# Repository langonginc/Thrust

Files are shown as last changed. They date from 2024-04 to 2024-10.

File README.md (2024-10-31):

# Horizontal Thrust Measuring Stage

A stage to measure horizontral thrust generated by rocket engine.

This is a project created by students in The Aviation Club of the [Second High School Attached to Beijing Normal University](https://www.shsbnu.net/index.html).

[推力台说明手册(中文版) | Chinese version](https://github.com/langonginc/Thrust/blob/main/README.pdf)

SolidWorks 3D Model

[Video from bilibili](https://www.bilibili.com/video/BV1fC411E7s8/?share_source=copy_web&vd_source=09f47ca71ce9a13b053114acdf5cffeb) 

# Highlights

We use Arduino Mega 2560 and HX711 to record and store the magnitude of the thrust into the program, and graph the associated function (force @ time).

- **0-20kg** measuring range _(maximum value not to exceed 30kg)_
- 30-50mm engine diameter fit
- 10Hz sample rate ([#1](https://github.com/langonginc/ForceTestStand/issues/1) We really need your help to increase it)
- Real-time display
- Serial port writing
- ~~SD card data writing~~

# Theory

Presure -> Sensors -> HX711 -> Arduino.

Pressure sensors generate a voltage by sensing pressure. Sensitive voltage value is 1mv, which means if I apply a force of `1kg`, it produces a voltage of `1mV` (for 0-10kg sensor).

HX711 will firstly amplify the voltage generated by the pressure sensor, since the voltage is too small. Then it will convert the analog signals (amplified voltage values) to digital signals (ad values).

After that, Arduino will get the digital signals (ad values). We then scale the digital signal to fit the pressure.

## Why We Use HX711

Based on Avia Semiconductor’s patented technology, HX711 is a precision 24-bit analog-to-digital converter (ADC) designed for weigh scales and industrial control applications to interface directly with a bridge sensor.

The input multiplexer selects either Channel A or B differential input to the low-noise programmable gain amplifier (PGA). Channel A can be programmed with a gain of 128 or 64, corresponding to a full-scale differential input voltage of ±20mV or ±40mV respectively, when a 5V supply is connected to AVDD analog power supply pin. Channel B has a fixed gain of 32. On-chip power supply regulator eliminates the need for an external supply regulator to provide analog power for the ADC and the sensor. Clock input is flexible. It can be from an external clock source, a crystal, or the on-chip oscillator that does not require any external component. On-chip power-on-reset circuitry simplifies digital interface initialization.

There is no programming needed for the internal registers. All controls to the HX711 are through the pins.

> We are using the channel A (input voltage of ±20mV).

## How HX711 works

The HX711 communicates with the microcontroller in serial communication mode consisting of pins SCK and DOUT. When DOUT goes from high to low, SCK inputs 25 pulses at a time to read the 24-bit A/D conversion data into the microcontroller and selects the input channel and gain for the next conversion on the 25th clock pulse.

# Getting Started

## Building Framework

Based on the Solidworks 3D model, the framework can be built with the following items.

| Item | Details | Quantity | Image |
| :----- | :----- | :----- | :----: |
| European Standard Aluminum Profiles 3030 | Length 400mm | 2 |  |
| European Standard Aluminum Profiles 3030 | Length 360mm | 1 | Same as above |
| European Standard Aluminum Profiles 3030 | Length 300mm | 5 | Same as above |
| European Standard Aluminum Profiles 3030 | Length 200mm | 1 | Same as above |
| European Standard Slider Nuts 3030 | M4 | About 20 |  |
| European Standard Angle Fittings 3030 | | 16 |  |
| Steel shaft ø8 | 300mm | 2 |  |
| Shaft fixing bracket ø8 | | 4 |  |
| Carriage slider ø8 | | 4 |  |
| Tray base plate _(Laser cut by myself)_ | From `plate.dwg` | 1 |  |

> SolidWorks 2022, AutoCAD 2024 (DWG 2018)

## Wiring the Arduino Board

Wire the Arduino board and components using DuPont wires according to the following table.

| Item | Image | Reference link |
| :----- | :----- | :----- |
| HX711 chip + Pressure sensor |  | [Link](https://detail.tmall.com/item.htm?id=570644601916) |
| TM1650 4-digit digital tube display module |  | |

**Arduino - HX711**

| Arduino Pin | HX711 Pin |
| :----: | :----: |
| 5V | VCC |
| GND | GND |
| 2 | SCK |
| 3 | DOUT |

**HX711 - Pressure sensors**

| HX711 Pin | Sensors Wire |
| :----: | :----: |
| E+ | Red |
| E- | Black |
| A- | White |
| A+ | Green |

**Arduino - Micro SD Card Adapter**

_We just removed this component as its low writing speed._

| Arduino Pin | HX711 Pin |
| :----: | :----: |
| 5V | VCC |
| GND | GND |
| 50 | MISO |
| 51 | MOSI |
| 52 | SCK |
| 53 | CS |

> The communication between the microcontroller and the SD card uses SPI, which takes place on digital pins 11, 12, and 13 (on most Arduino boards) or 50, 51, and 52 (Arduino Mega). Additionally, another pin must be used to select the SD card. This can be the hardware SS pin - pin 10 (on most Arduino boards) or pin 53 (on the Mega) - or another pin specified in the call to SD.begin(). Note that even if you don't use the hardware SS pin, it must be left as an output or the SD library won't work.
>
> --Arduino SD libarary

## Uploading Code to Arduino Board

Download `main.ino` and open it in Arduino IDE ([Link](https://www.arduino.cc/en/software)).

Plug in your Arduino. Then, click the "upload" button.

## Getting Data

Click `Tools - Serial Monitor` to check the results.



## Analysing Data

Copy the results getting from the serial monitor, which are array of integers (e.g. `101, 123.4, 111, 114.5, 121, 514.5, ...`) to the third line of `graph.py`.

```python
originalData = [ Paste Data To Here ]     # Notice: delete the last comma ',' !!!
```

Run the code, you will get a graph that is the associated function (force @ time).

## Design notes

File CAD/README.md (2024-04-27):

# CAD files

These files are written with AutoCAD 2024 and saved in format DWG 2018.

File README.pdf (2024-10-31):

北京师范⼤学第⼆附属中学 航模社 | ⽔平推⼒测定台 v1.4

# ⽔平推⼒测定台说明⼿册

# 任务要求

实现 10 公⽄⽔平推⼒精确测定，通过推⼒数据绘制⼒关于时间（F/t）图像。

# 实现思路

使⽤欧标 3030 铝⽅管作为框架材料，将 304 不锈钢材质托盘放置在滑轨上，并 将产⽣推⼒的物品通过夹具固定在托盘上。产⽣推⼒时，带动滑块向前推测⼒计进⾏ 测⼒。测⼒计由 10 公⽄测⼒模块组成，使⽤ Arduino + HX711 模块处理数据，并使⽤ Python 程序⽣成相关图像。

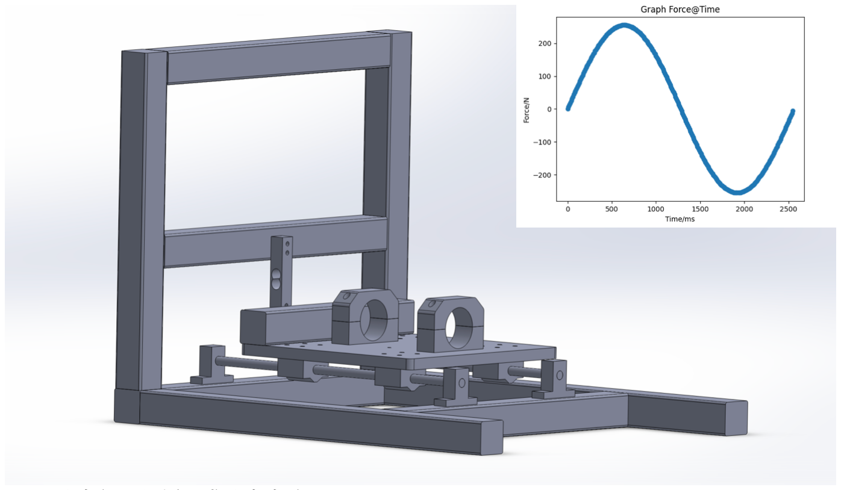
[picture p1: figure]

测试台还包括两盏⼤灯提供照明。

# 物品清单

铝⽅管
欧标 3030 400mm | 2 个
欧标 3030 360mm | 1 个
欧标 3030 300mm | 5 个
欧标 3030 200mm | 1 个
欧标 3030 直⻆连接⻆件 | 16 套
欧标 3030 滑块螺⺟ | ⽀架 8+托盘前挡 2+测⼒计前板 2+侧板 2 个
欧标 3030 端盖 | 8 个

轴
钢制轴 ø8 300mm | 2 根 | 有
轴固定⽀架 ø8 | 4 个
厢式滑块 ø8 | 4 个
限位器 ø8 | 1 个

螺丝
M4*10（滑块） | 16 根
M4*10（固定⽀架） | 8 根
M4*15（前挡） | 1 根

电路元件
测⼒计（含 HX711） | 1 套
Arduino Mega 2560 | 1 个
Arduino Micro SD 卡组件 | 1 个 | 删去，保留拓展能⼒
数码管显示屏 | 1 个
杜邦线 | 若⼲

夹具
夹具（3D 打印） | 2 套

灯具
灯具（遮光罩 3D 打印） 2 套

其他⾃制
托盘（⽊板/亚克⼒） | 1 个 | 切割
前档板 | 1 个 | 切割
测⼒计防撞板 | 1 个 | 切割

# 实现技术参数

⻓宽⾼ | 430*360*330
承重能⼒ | 约 50kg
测量推⼒范围 | 0.02kg-20kg
最⼤安全推⼒ | 30kg
承载物直径 | 38-52mm
承载物⻓度（建议） | 40-200mm
承载物⻓度（理论最⼤） | 300mm
理论最⼩采样率 | 10ms/次
实际采样率 | 100ms/次

# 原理解释

由压⼒传感器采集信号，并通过 HX711 芯⽚信号放⼤、AD 转换实现⽤数字信号 输⼊进 Arduino 单⽚机进⾏处理，最终将数据存储并显示。
HX711 是⼀款专为⾼精度电⼦秤⽽设计的 24 位 A/D 转换器芯⽚。与同类型其它 芯⽚相⽐，该芯⽚集成了包括稳压电源、⽚内时钟振荡器等其它同类型芯⽚所需要的 外围电路，具有集成度⾼、响应速度快、抗⼲扰性强等优点。降低了电⼦秤的整机成 本，提⾼了整机的性能和可靠性。该芯⽚与后端 MCU 芯⽚的接⼝和编程⾮常简单， 所有控制信号由管脚驱动，⽆需对芯⽚内部的寄存器编程。输⼊选择开关可任意选取 通道 A 或通道 B，与其内部的低噪声可编程放⼤器相连。通道 A 的可编程增益为 128 或 64，对应的满额度差分输⼊信号幅值分别为±20mV 或±40mV。通道 B 则为固定的 64 增益，⽤于系统参数检测。芯⽚内提供的稳压电源可以直接向外部传感器和芯⽚内 的 A/D 转换器提供电源，系统板上⽆需另外的模拟电源。芯⽚内的时钟振荡器不需要 任何外接器件。上电⾃动复位功能简化了开机的初始化过程。
HX711 与单⽚机的通讯由管脚 SCK 和 DOUT 组成的串⾏通讯模式。当 DOUT 从 ⾼电平变成低电平后，SCK ⼀次输⼊ 25 个脉冲，将 24 位 A/D 转换数据读⼊单⽚机， 并在第 25 个时钟脉冲选择好下次转换的输⼊通道和增益。
使⽤⽅法

打开 Arduino IDE 的串⼝监视器，并向 Arduino 通电，等待显示屏显示“8888”，此 时系统初始化完毕。
轻推测⼒计⼀下，使屏幕显示“0000”。松开后，屏幕会开始倒计时 3 秒。等到显 示“0”时，开始测⼒。
将产⽣推⼒的物体⽔平推测⼒计，当测⼒计记录到⼒时，屏幕会显示⼒的⼤⼩， 当⼒⼩于 10000g 时单位为克（g），超过时显示单位为千克（kg），此时会向 SD 卡内 写⼊数据。
测⼒完成后，相反⽅向拉动测⼒模块，使之产⽣超过负 1000 克的⼒，然后切断 电源即可。

# 总结反思

当前版本已经过⼿压⼒测试，考核范围 0-33kg，顺利通过。 本产品出⾊地完成了推⼒测定任务，在 1.5s 内完成了 16 个采样（左图），绘制出 了拟合曲线，并进⾏了积分运算，得出了推⼒曲线（右图）。

数据采集

AD 转换 | 单⽚机处理 | 数码管显示 串⼝输出
信号放⼤

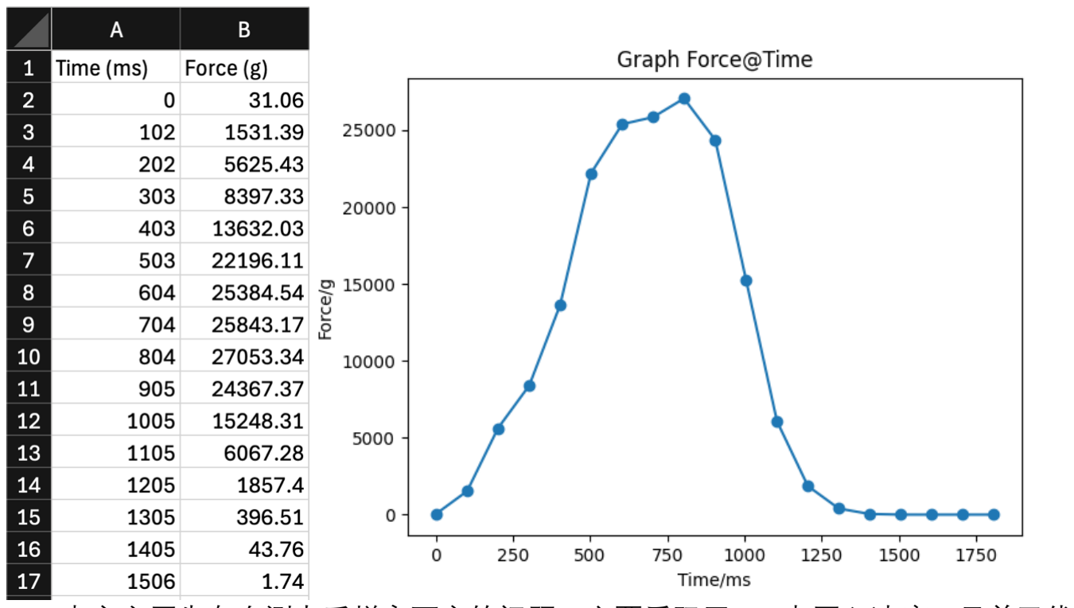
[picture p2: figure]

本⽅案原先存在测⼒采样率不⾼的问题，主要受限于 SD 卡写⼊速度，⽬前已优 化，仅使⽤串⼝通信⽅案。⽽串⼝通信⽅案的弊端在于应⽤时必须使⽤电脑有线连接 本产品，不如原⽅案便捷。

# 附加信息

本设计⽅案由北京师范⼤学第⼆附属中学航模社设计实施，以上内容仅供参考。 本设计⽅案同时发布于 GitHub 平台，在 langonginc/ForceTestStand (https://github.com/langonginc/ForceTestStand) 仓库托管，基
于 GPL-3.0 协议开源，修改或商⽤需遵守 GPL-3.0 协议的规定。

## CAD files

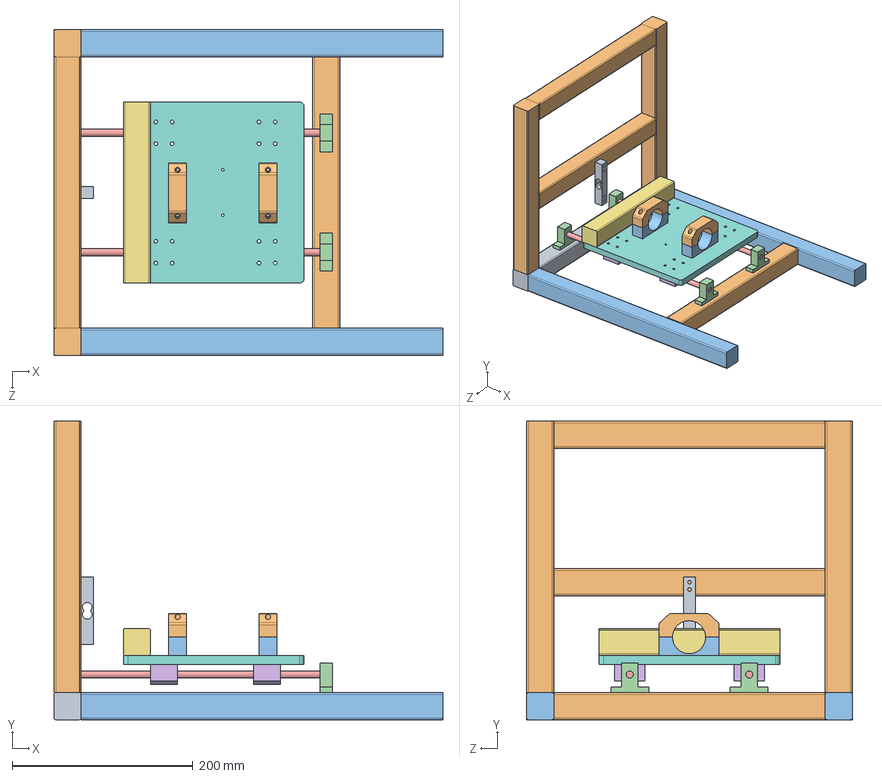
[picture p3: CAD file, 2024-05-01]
SolidWorks 3D Model/platform.SLDASM
430.0 x 330.0 x 360.0 mm
3030M-2-360
3030M-2-300 x 5
3030M-2-400 x 2
foot-8 x 4
stick-8-400 x 2
slider x 4
3030M-2-200
plate-new
sensor
fixture-upper x 2
fixture-lower x 2

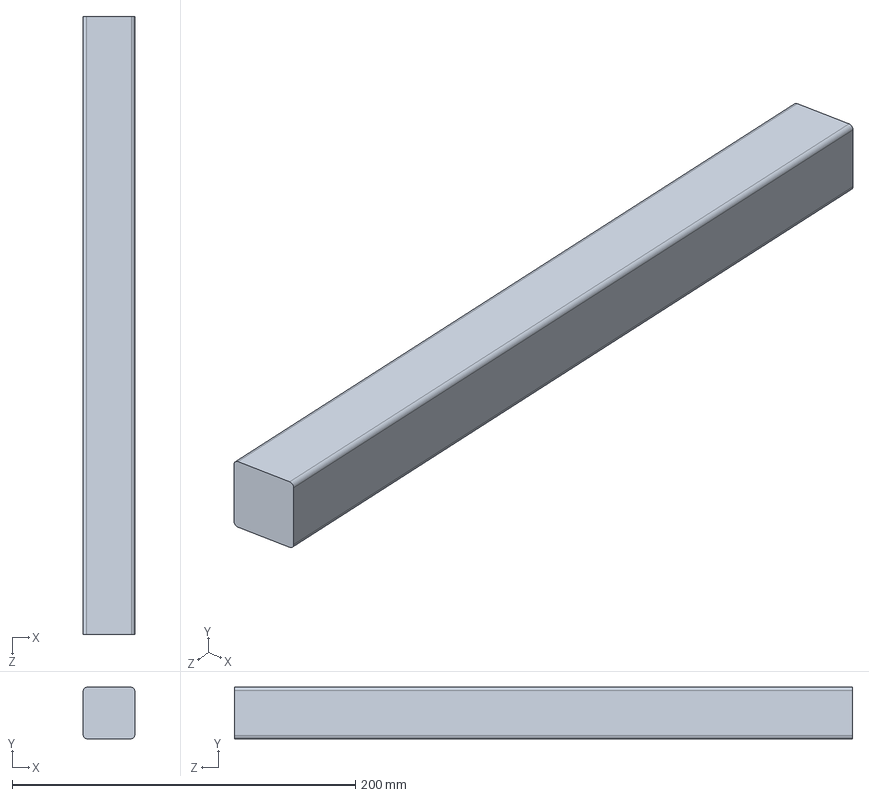
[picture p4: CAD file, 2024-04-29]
SolidWorks 3D Model/3030M-2-360.SLDPRT
30.0 x 30.0 x 360.0 mm

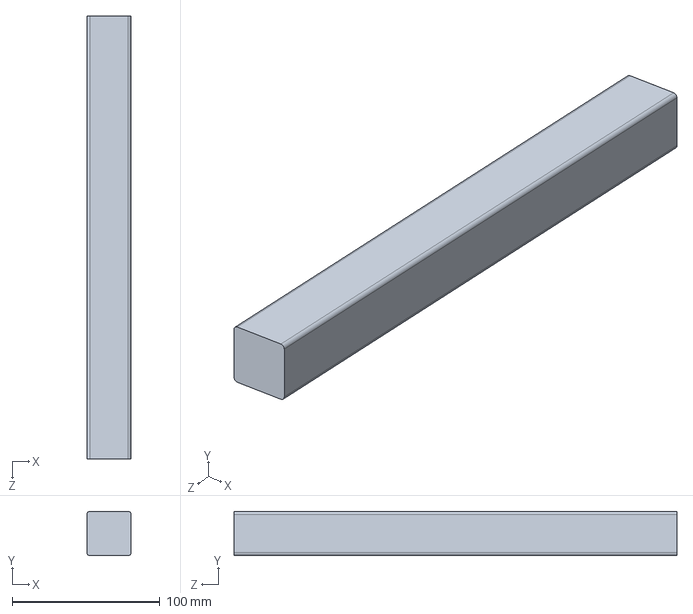
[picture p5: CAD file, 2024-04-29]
SolidWorks 3D Model/3030M-2-300.SLDPRT
30.0 x 30.0 x 300.0 mm

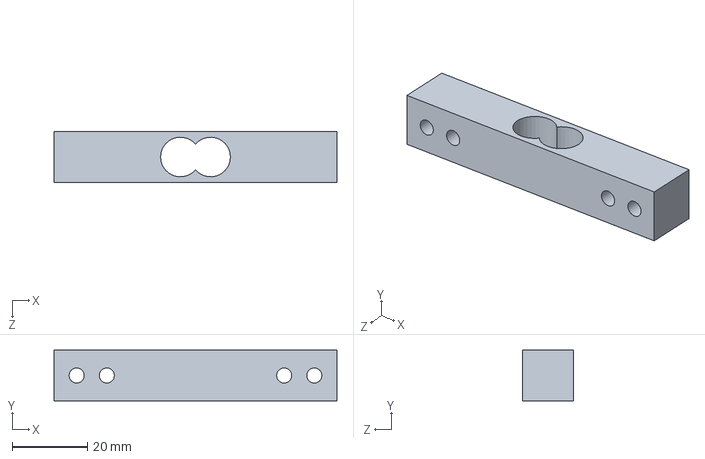
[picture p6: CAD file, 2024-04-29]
SolidWorks 3D Model/sensor.SLDPRT
75.0 x 13.5 x 13.5 mm

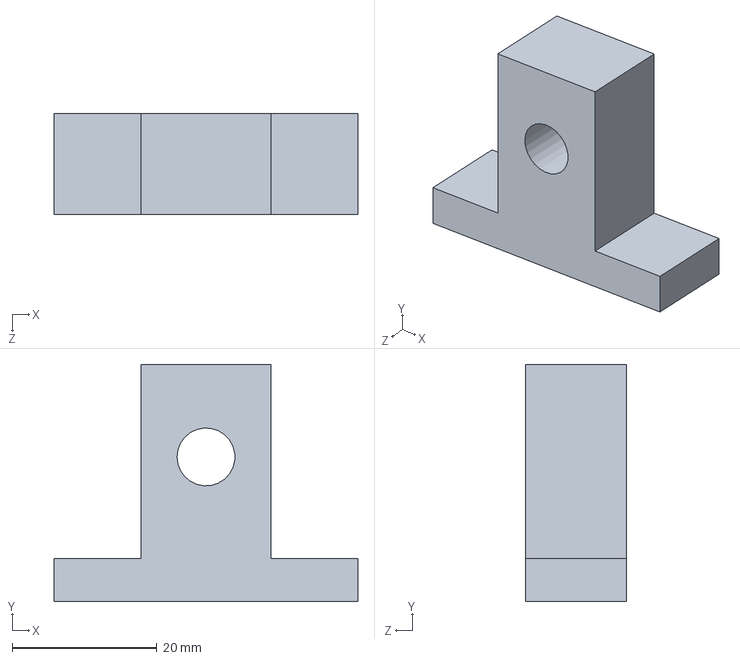
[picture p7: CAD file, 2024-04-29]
SolidWorks 3D Model/foot-8.SLDPRT
42.0 x 32.8 x 14.0 mm

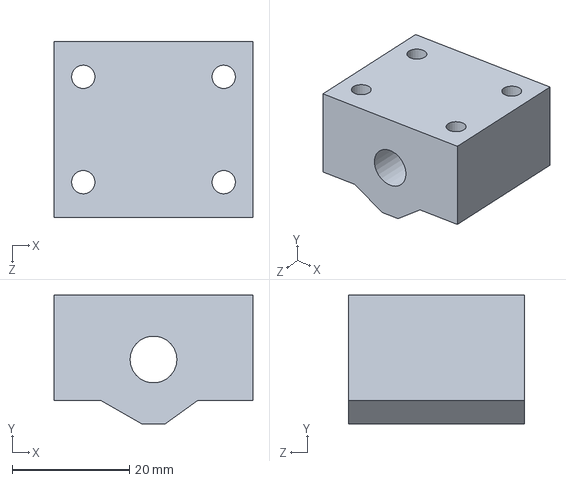
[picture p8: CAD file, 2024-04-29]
SolidWorks 3D Model/slider.SLDPRT
34.0 x 22.0 x 30.0 mm

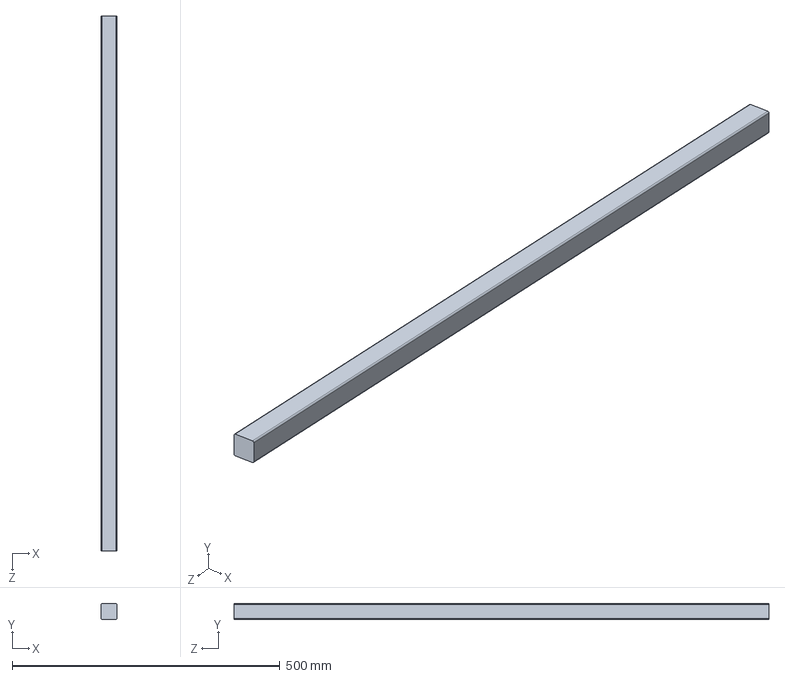
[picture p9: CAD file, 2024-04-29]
SolidWorks 3D Model/3030M-2-1m.SLDPRT
30.0 x 30.0 x 1000.0 mm

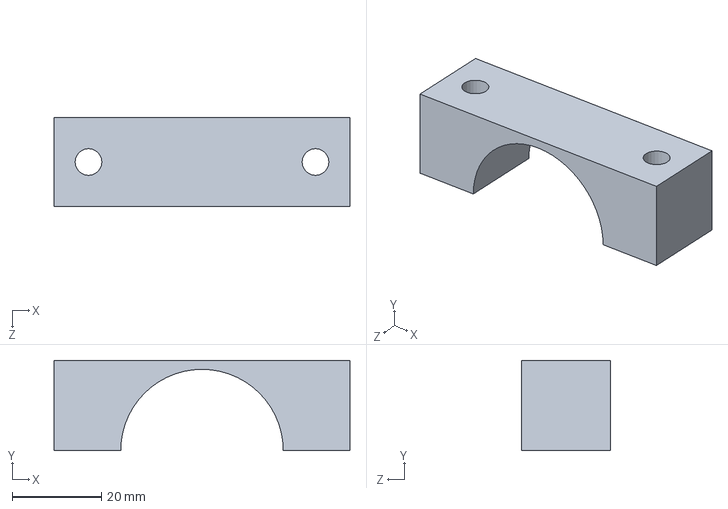
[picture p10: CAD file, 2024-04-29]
SolidWorks 3D Model/fixture-lower.SLDPRT
66.5 x 20.2 x 20.0 mm

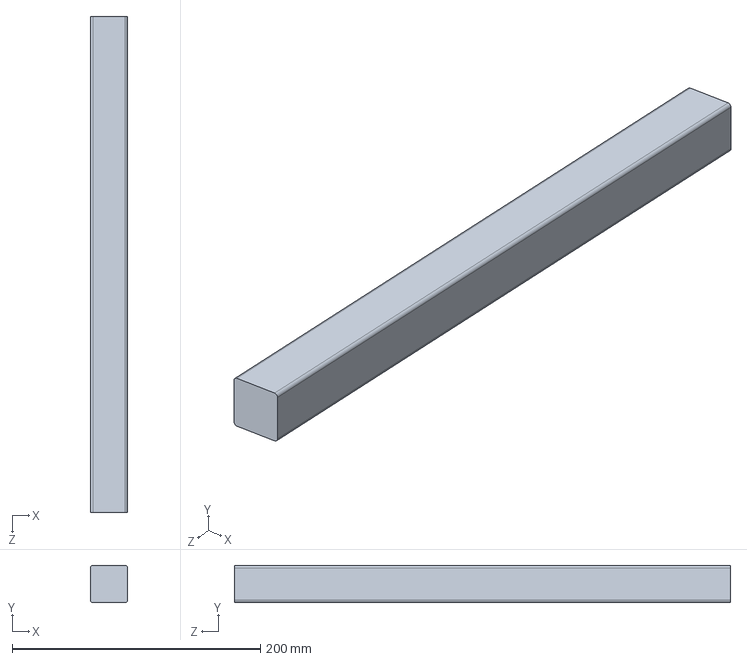
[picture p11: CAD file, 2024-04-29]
SolidWorks 3D Model/3030M-2-400.SLDPRT
30.0 x 30.0 x 400.0 mm

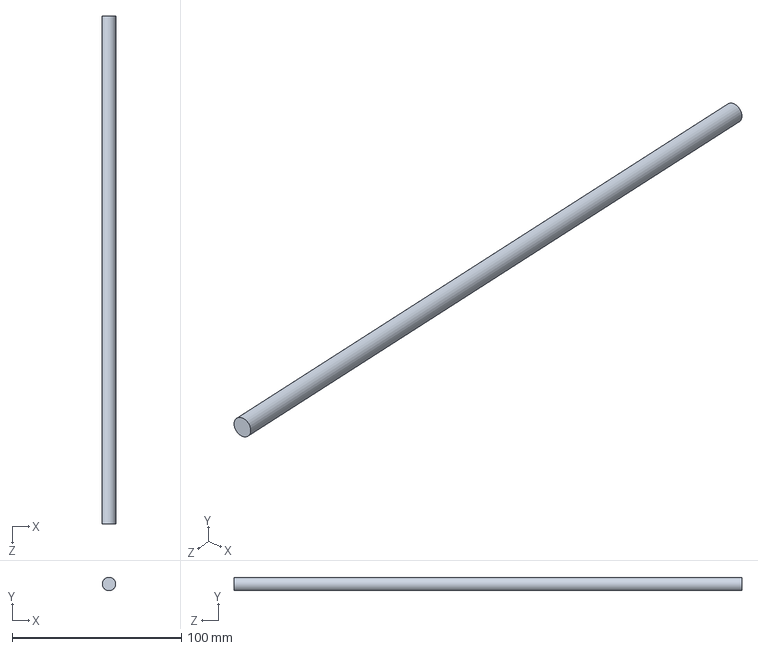
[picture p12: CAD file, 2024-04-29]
SolidWorks 3D Model/stick-8-400.SLDPRT
8.00 x 7.94 x 300.0 mm

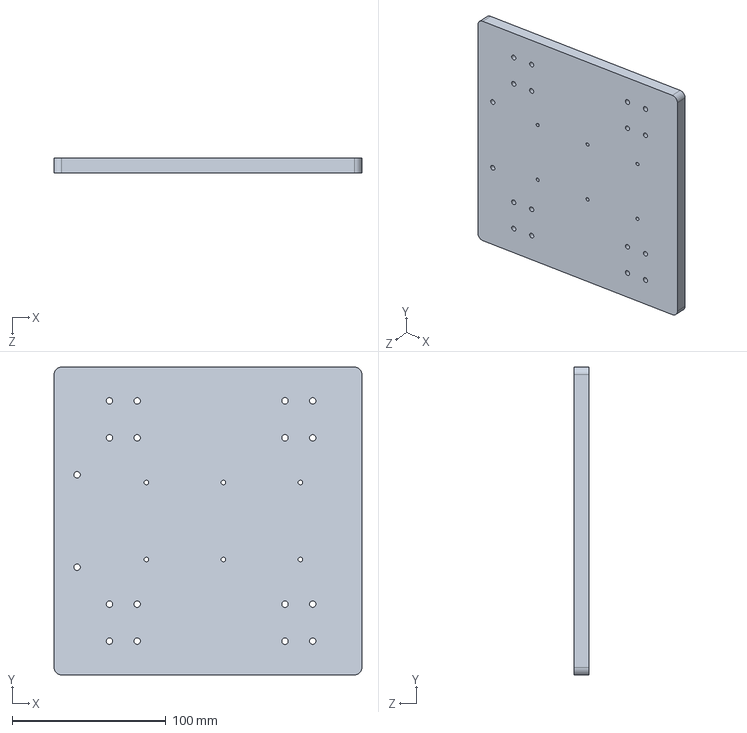
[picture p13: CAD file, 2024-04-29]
SolidWorks 3D Model/plate-new.SLDPRT
200.0 x 200.0 x 10.0 mm

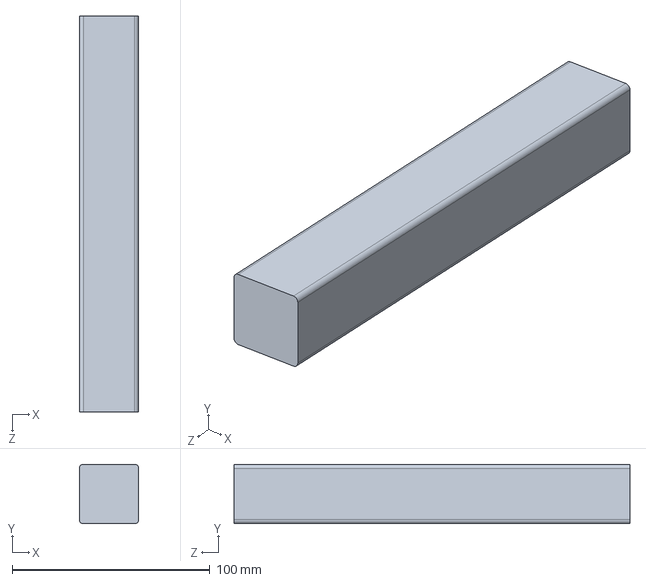
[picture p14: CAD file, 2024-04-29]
SolidWorks 3D Model/3030M-2-200.SLDPRT
30.0 x 30.0 x 200.0 mm

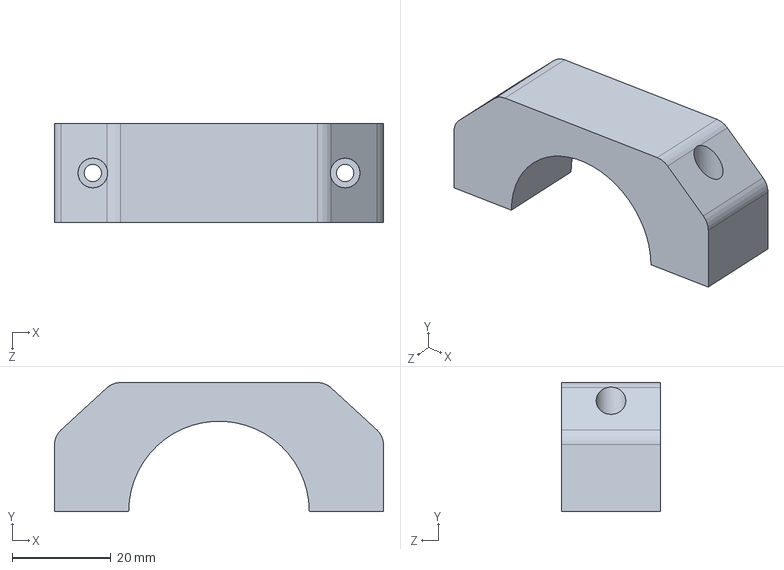
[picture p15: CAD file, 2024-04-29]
SolidWorks 3D Model/fixture-upper.SLDPRT
66.5 x 26.1 x 20.0 mm

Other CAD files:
CAD/plate.dwg

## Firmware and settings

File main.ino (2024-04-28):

/*
 Horizontal Thrust Measuring Stage (https://github.com/langonginc/Thrust)
 by Jiayi Wu (@langonginc)
  - The Aviation Club of the Second High School Attached to Beijing Normal University

 Last modified: 2024/04/28

* HX711
 Arduino pin 2 -> HX711 SCK (CLK)
 3 -> DT (D_OUT)
 5V -> VCC
 GND -> GND

* SD
 5V -> 5V
 GND -> GND
 CS -> 4
 MOSI -> 11
 SCK -> 13
 MISO -> 12
*/

#include <HX711.h>
// #include <SPI.h>
// #include <SD.h>
#include <Wire.h>
#include <TM1650.h>

#define calibration_factor -11181
#define zero_factor 8421804

#define SAMPLE_RATE  50

#define DOUT  3
#define CLK  2
#define CHIP_SELECT  53
#define LED  LED_BUILTIN

HX711 scale;
// File dataFile;
TM1650 display;

enum Status {
  Ready,
  Activating,
  Init,
  Working,
  Done
} status;
bool LedStatus;

/*
* Error List
* 1: SD card init failed - *Removed
* 2: File cannot be read (e.g. the file is read-only)
*/
void error (int id) {
  String str = String("E") + String(id);
  if (getK(id) == 1) {
    str = str + String("  ");
  } else if (getK(id) == 2) {
    str = str + String(" ");
  }
  display.displayString(str.c_str());
}

void setup() {
  status = Init;

  /* System Setup */
  Serial.begin(9600);
  Serial.println("Starting...");
  pinMode(LED, OUTPUT);
  LedStatus = false;

  /* Display Setup */
  Wire.begin(); //Join the bus as master
  display.init();
  display.displayOn();
  display.setBrightnessGradually(0);

  /* HX711 Setup */
  scale.begin(DOUT, CLK);
  scale.set_scale(calibration_factor); //This value is obtained by using the SparkFun_HX711_Calibration sketch
  scale.tare();	//Reset the scale to 0
 // scale.set_offset(zero_factor); //Zero out the scale using a previously known zero_factor

  /* SD Setup */
  /* SD card was dropped in version 1.3
  if (!SD.begin(CHIP_SELECT)) {
    Serial.println(F("SD card initialization failure. Exit..."));
    error(1);
    delay(1000);
    exit(1);
    return;
  }
  dataFile = SD.open("data.txt", FILE_WRITE);
  if (!dataFile) {
    Serial.println(F("Data file cannot be open. Exit..."));
    error(2);
    delay(1000);
    exit(1);
    return;
  }
  */

  Serial.println("Started~");

  status = Ready;
  display.displayString("8888");
}

inline void HiLed () {
  if (!LedStatus) {
    digitalWrite(LED, HIGH);
    LedStatus = true;
  }
}

inline void LoLed () {
  if (LedStatus) {
    digitalWrite(LED, LOW);
    LedStatus = false;
  }
}

inline int getK (int val) {
  if (val < 0) return 0;
  if (0 <= val && val < 10) return 1;
  if (10 <= val && val < 100) return 2;
  if (100 <= val && val < 1000) return 3;
  if (1000 <= val && val < 10000) return 4;
}

inline String getDisplayStr (int value) {
  String originNum = String(value);
  for (int i = 0; i < 4 - getK(value); i ++) {
    originNum = String("0") + originNum;
  }
  return originNum;
}

// Default as value (g).
// if value > 9999 -> output as XX.XX (kg)
inline void displayValue (int value) {
  if (0 <= value && value < 10000) {
    display.displayString(getDisplayStr(value).c_str());
  } else if (value < 1000000) {
    display.displayString(getDisplayStr(value / 10).c_str());
    display.setDot(0, true);
  } else {
    error(3);
  }
}

inline void writeData (unsigned long t, double f) {
  /* SD card part was dropped in version 1.3
  dataFile.print(t);
  dataFile.print(", ");
  dataFile.print(f);
  dataFile.print(", ");
  */

  Serial.print(t);
  Serial.print(", ");
  Serial.print(f);
  Serial.print(", ");
}

unsigned long startTime = 0;
unsigned long countTime = 0;

void loop() {
  unsigned long t = millis();
  double value = scale.get_units() * 100;
  int valInt = int(value);
  if (false) { // DEBUG -> set it to true !!!
    Serial.print(status);
    Serial.print(" ");
    Serial.println(value);
  }
  switch (status) {
    case Ready:
      HiLed();
      if (valInt > 10) {
        LoLed();
        status = Activating;
        break;
      }
      delay(100);
      break;
    case Activating:
      if (valInt <= 0) {
        status = Working;
        display.displayString("3   ");
        HiLed();
        delay(1000);
        LoLed();
        delay(200);
        display.displayString("2   ");
        HiLed();
        delay(1000);
        LoLed();
        delay(200);
        display.displayString("1   ");
        HiLed();
        delay(1000);
        LoLed();
        display.displayString("   0");
     } else {
        display.displayString("0000");
      }
      break;
    case Working:
      if (valInt > 0) {
        if (startTime == 0) {
          HiLed();
          startTime = t;
          countTime = t;
        }
        if (t - countTime >= SAMPLE_RATE) {
          countTime = t;
          writeData(t - startTime, value);
          displayValue(valInt);
        }
      }
      if (valInt < -1000) {
        LoLed();
        // dataFile.println("");
        // dataFile.close();
        display.displayString("8888");
        Serial.println("<-");
        Serial.println("Exit with code 0.");
        exit(0);
      }
      break;
    case Done:
      break;
  }
}

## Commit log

2024-04-27 Add TM1650 4-digit digital tube display module
2024-04-27 Add plate.dwg
    [plate.dwg]
2024-04-29 Add SolidWorks 3D Model
    [3030M-2-1m.SLDPRT, 3030M-2-200.SLDPRT, 3030M-2-300.SLDPRT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]
2024-05-01 Add assembly
    [platform.SLDASM]
